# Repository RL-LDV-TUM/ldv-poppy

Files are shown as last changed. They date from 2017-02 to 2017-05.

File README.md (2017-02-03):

# LDV Poppy

The LDV Poppy is a customized version of the [Poppy Humanoid](https://www.poppy-project.org/en/robots/poppy-humanoid) by poppy-project.
The original Github repository containing the Solidworks 3D files and Software can be found [here](https://github.com/poppy-project/poppy-humanoid).
There is also a Onshape project where all Solidworks files are imported: [Poppy humanoid v1.0.1](https://cad.onshape.com/documents/77a0f84dc57f40418500cc3e/w/5e73b9c6a1ca45368c6251fc/e/ed6b82f994b249e388f92c2e).
This Onshape project can be cloned and edited. However it is sometimes easier to import only single Solidworks files from this repository to onshape.

## 3D Models

The Onshape project for the [LDV Poppy can be found here.](https://cad.onshape.com/documents/56d596aee4b004367d90f087/w/5446e589942f217504b25eb7/e/aac52fdb51e2f46d7fa4375f).
This project contains a full clone of the original Onshape project and the optimized files. Optimizations were nescessary to improve the 3D print outcome
on the Renforce RF1000 3D-Printer available at the LDV.
Currently there are still parts which need a redesign or can only be printed in a certain orientation: [Errors and Defects](3D/defects.md)

Instructions for printing can be found [here](3D/print.md).
Solidworks source files for editing: [solidworks](3D/solidworks)
STL files for printing: [stl](3D/stl)

## Programming

Poppy provides his own websever: [poppy.clients.ldv.ei.tum.de](http://poppy.clients.ldv.ei.tum.de)

Several *jupyter* notebooks are provided to controll the robot using the *odroid* mini PC.

Connecting poppy to the network: [Network](Software/network.md)

Getting started with poppy: [Working with poppy](Software/gettingStarted.md)

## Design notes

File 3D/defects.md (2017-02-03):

# Broken Parts
Most parts have a very tight fit. Therefore, some narrow structures break when higher tension occures. This happens because the space for the motors is too small or
the weight of the robot is to high. 

## Knee
The knee split up at a very narrow cover of the motor. This does not effect the payload because the part is held together by the motor itself.
However the crack does not look very nice.
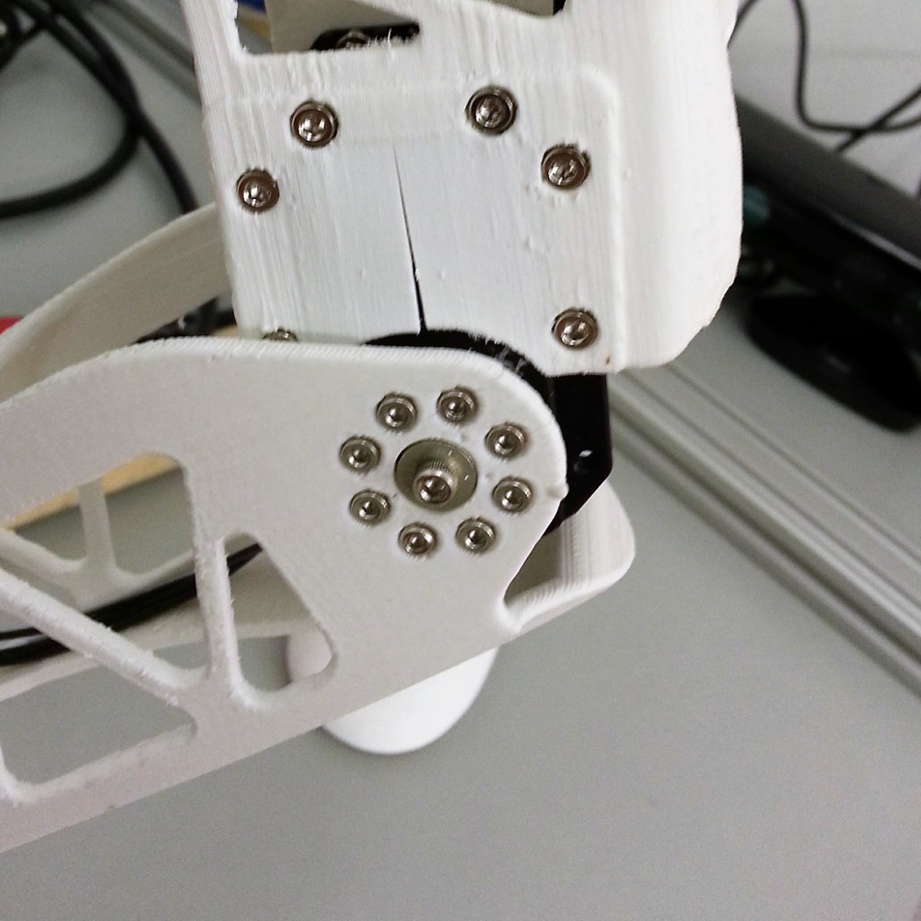
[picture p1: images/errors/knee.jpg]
Knee


On the other knee also the lower part has cracks in it. These were caused by the screws and an uneven print result.
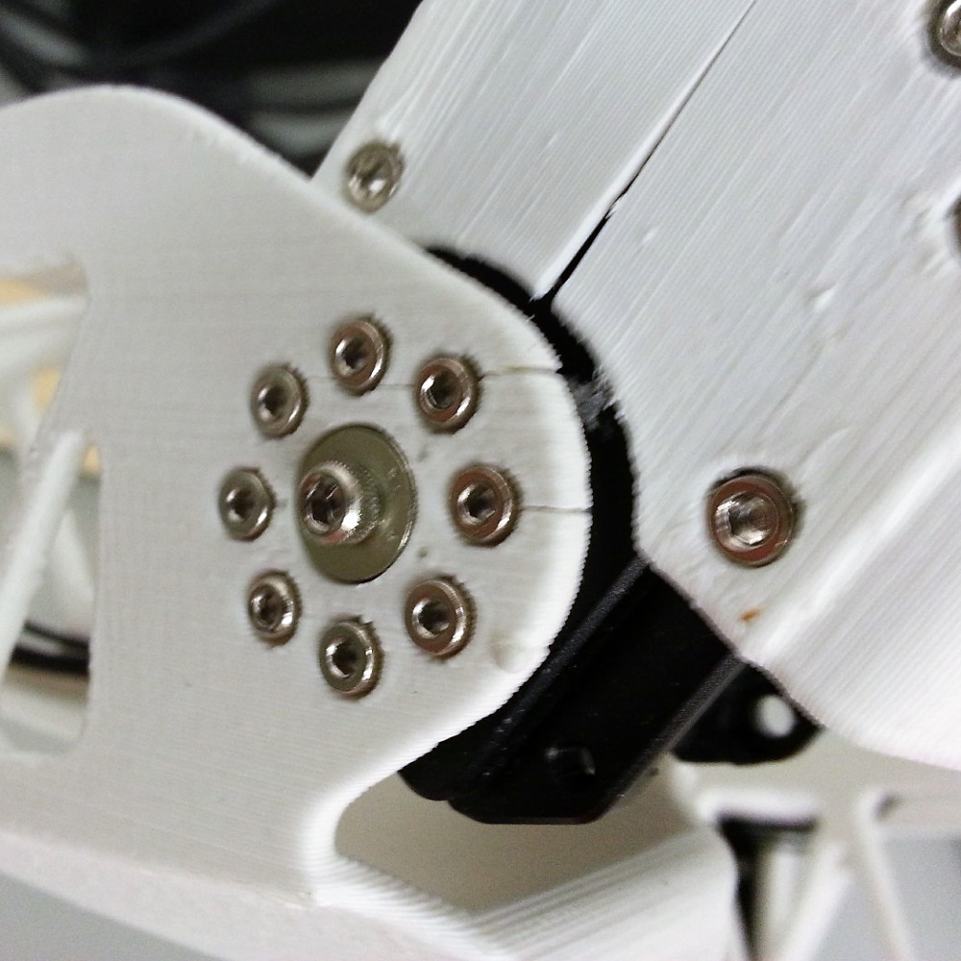
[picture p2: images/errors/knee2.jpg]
Knee2


## Ankle
The ankle has to be printed this way so that to motor plate fits through. Unfortunately, this causes the upper screws to be literally useless.
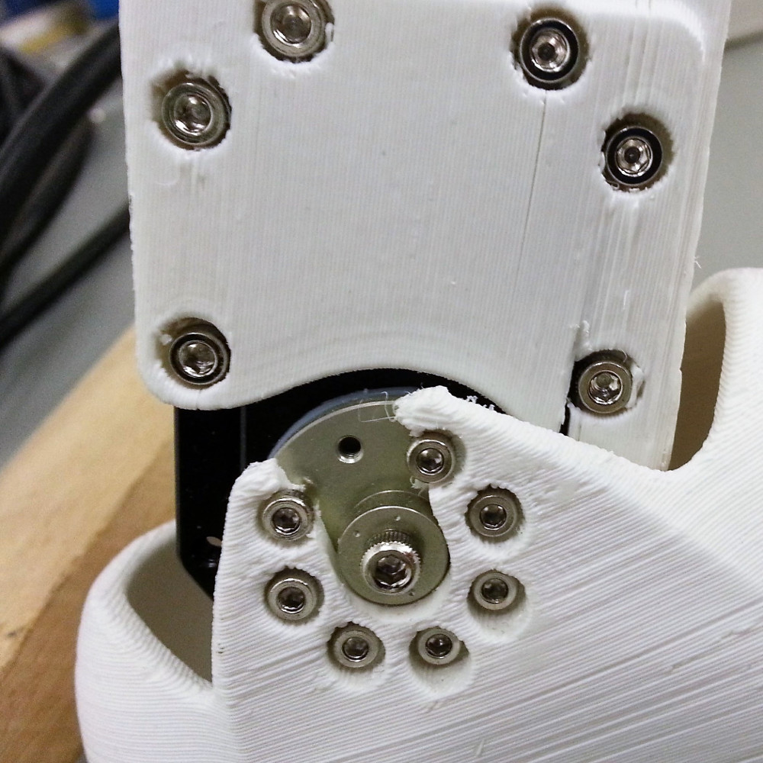
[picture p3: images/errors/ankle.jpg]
Ankle


## Pelvis
Due to hugh stress on this part, the pelvis broke in half at a printing layer. 
A new version of the pelvis is now employed in the robot which is 3mm thicker at each side.
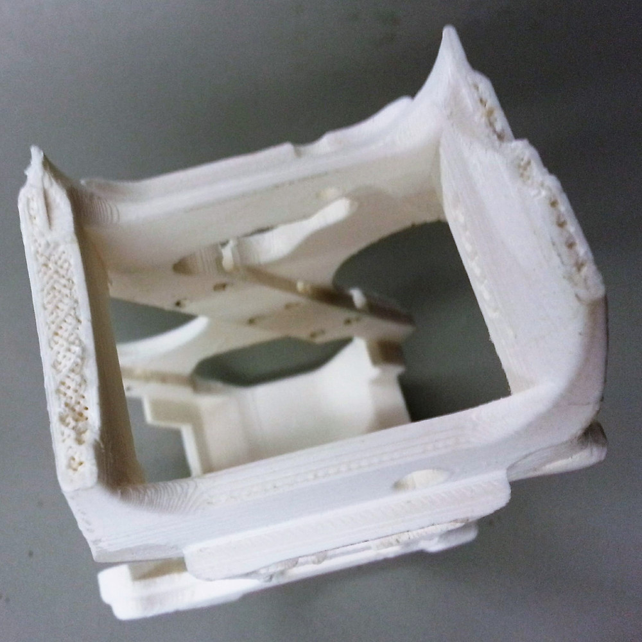
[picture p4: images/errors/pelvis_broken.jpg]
Pelvis


## Upper Arm
The upper arm suffered the same error as the knee. The narrow plate covering the motor was already thickened an reprinted.
The range of this plate is limited by the shouled part and can not be increased much further.

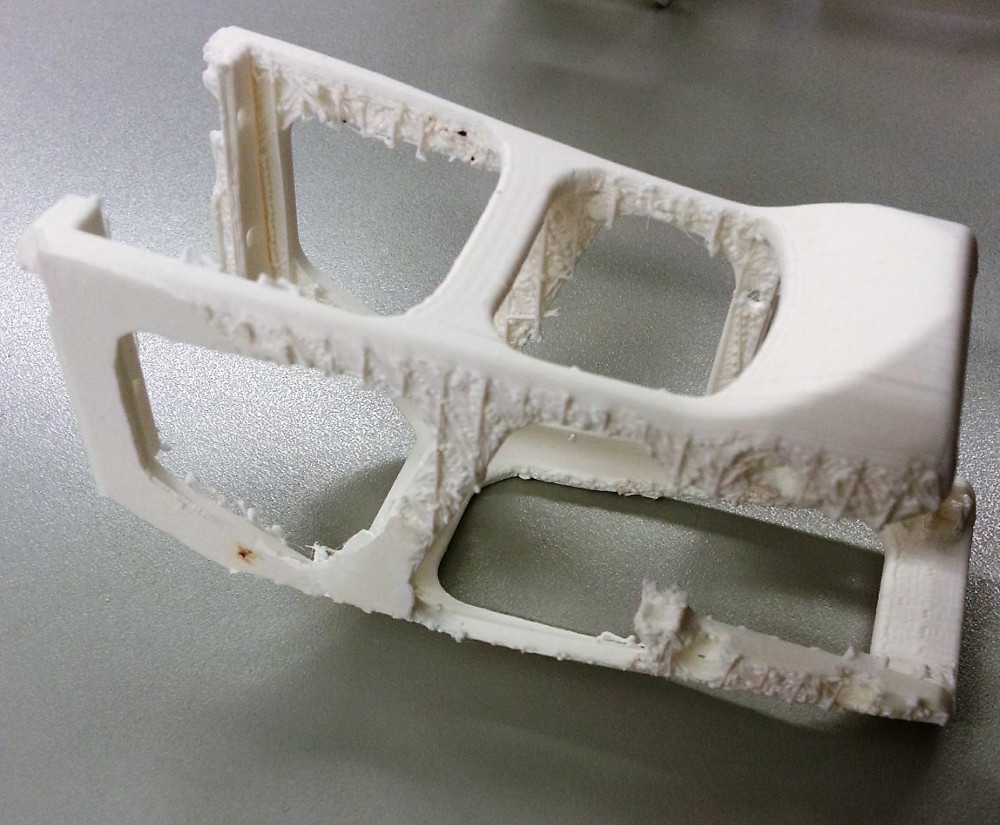
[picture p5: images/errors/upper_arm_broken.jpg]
Upper Arm


# Print Orientation
As the pelvis shows, printed parts are **vunerable where the filament layers are connected**. It is very unlikely that a layer itself will break.
Therefore, it is important that the object is printed in a way that later on no big forces will tear the different layers apart.
The main forces should never appear orthogonal to the layers, but alway **parallel**.

Unfortunately some parts are not feasable to be printed in that way.

## Chest
The chest is the biggest part of the robot. According to the forces it would be optimally printed standing upright.
Also the designers placed the grip in a way that the original model can not be printed lying without a huge amount of support strucutres.
The outcome of an upright print was not usable, so that the model had to be redesigned to be printed lying. 
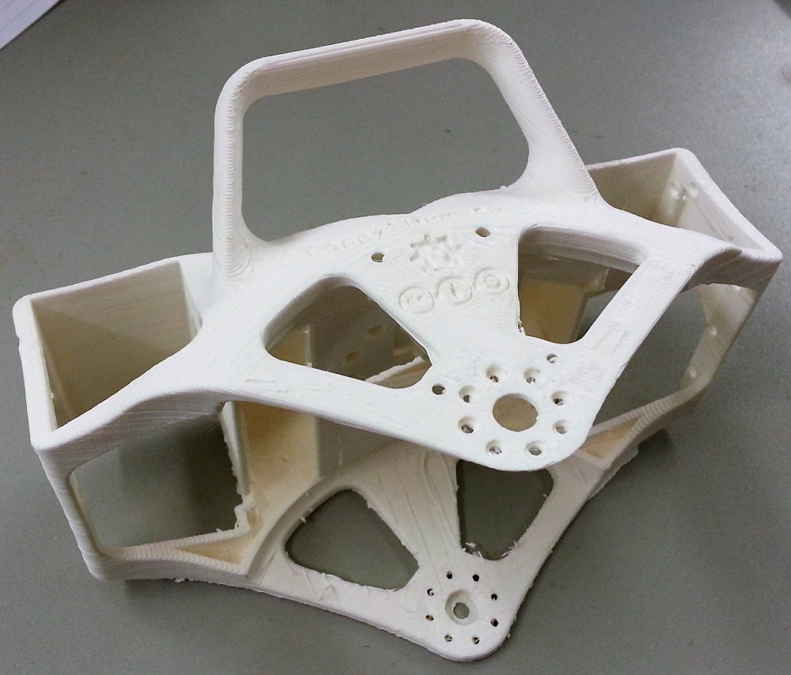
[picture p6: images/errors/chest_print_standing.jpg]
Chest

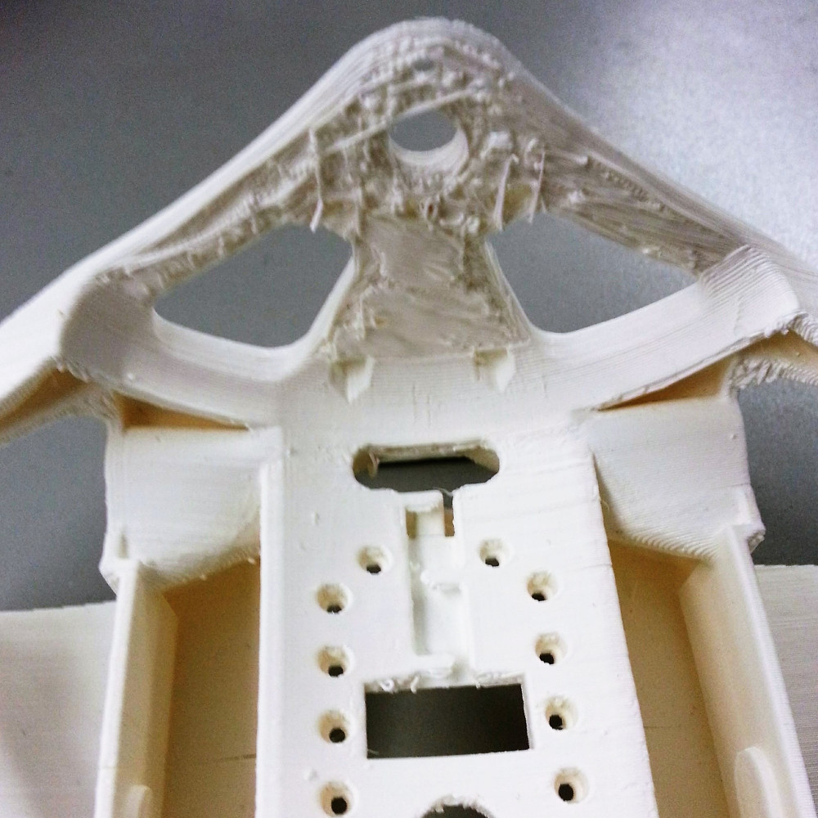
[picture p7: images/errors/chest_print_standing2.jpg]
Chest2


## Pelvis
The lying position has its advantages for the adhesion of the object.
The thin parts of the pelvis show that this is not feasable for this part.
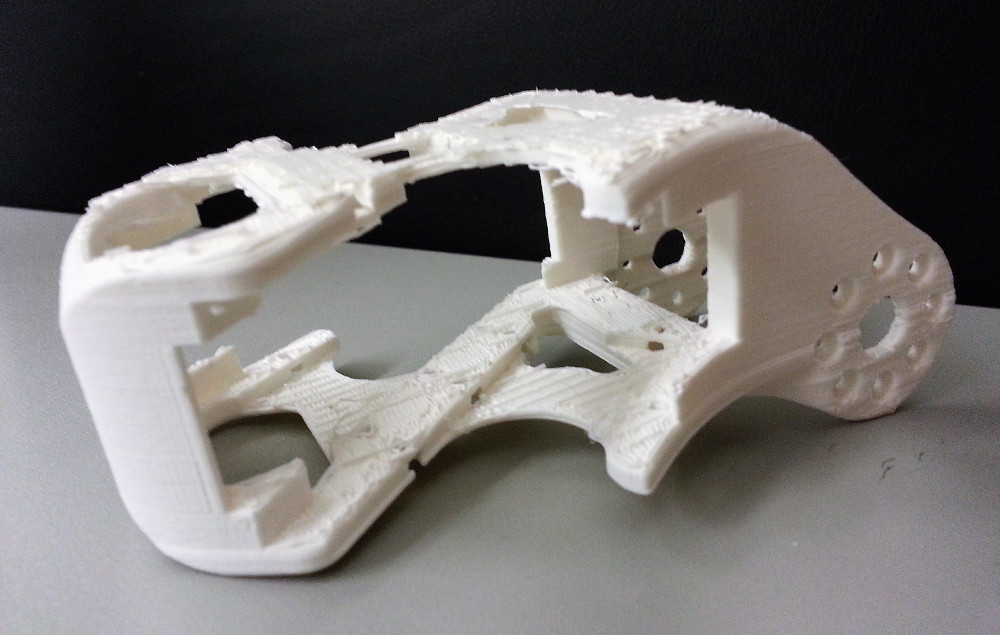
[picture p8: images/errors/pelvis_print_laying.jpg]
Pelvis


## Spine
One has to deal with the higher forces on the layers when the part is printed in the only possible standing position.
This can be done by increasing the thickness of the part where it does not affect the degrees of freedom of the motors.
The Spine before and after the increas of the outer walls.
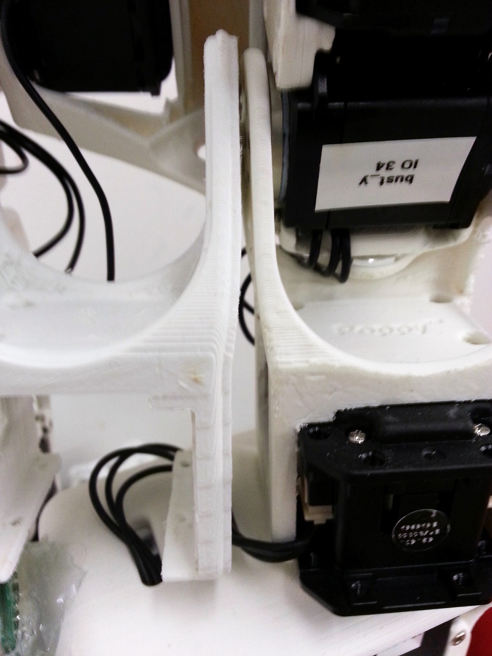
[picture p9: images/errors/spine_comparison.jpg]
Spine


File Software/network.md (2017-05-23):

# Ethernet

Poppy is configured to obtain a IP adress via DHCP when he is connected to the lrz network with an ethernet cable.
The DNS Service [poppy.clients.ldv.ei.tum.de](http://poppy.clients.ldv.ei.tum.de) is configured only for Wifi connections to the LDV-CPP network bridge.

# Wifi
Poppy automatically connects to the Wifi SSID: **LDV-CPP**

The LDV-CPP accesspoints work in bridge-mode so Poppy can be reached by: [poppy.clients.ldv.ei.tum.de](http://poppy.clients.ldv.ei.tum.de) 
This only works when the accesspoint is connected to the lrz network. 

    # interfaces(5) file used by ifup(8) and ifdown(8)
    # Include files from /etc/network/interfaces.d:
    source-directory /etc/network/interfaces.d
    
    auto eth2
    iface eth2 inet dhcp
    
    iface default inet dhcp
    
    auto lo
    iface lo inet loopback
    
    auto wlan2
    iface wlan2 inet dhcp
            wpa-ssid "LDV-CPP"
            wpa-psk "*******"
    
    allow-hotplug wlan2 eth2

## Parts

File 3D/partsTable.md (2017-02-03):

This table contains the settings which where used to print the current version of LDV-Poppy.

| 	| **Part Name** 	| **Resolution** 	| **Infill** 	| **Design Version** 	| **Units** 	| **Comment** 	|
|---	|---	|---	|---	|---	|---	|---	|
| **ARMS**  	| arm_connector 	| 0.2 	| 80 	| 1 	| 2 	| 	|
| 	| forearm_left 	| 0.2 	| 80 	| 1 	| 1 	| 	|
| 	| forearm_right 	| 0.2 	| 80 	| 1 	| 1 	| 	|
| 	| hand_left 	| 0.3 	| 80 	| 1 	| 1 	| 	|
| 	| hand_right 	| 0.3 	| 80 	| 1 	| 1 	| 	|
| 	| shoulder_left 	| 0.2 	| 80 	| 1 	| 1 	| 	|
| 	| shoulder_right 	| 0.2 	| 80 	| 1 	| 1 	| 	|
| 	| upper_arm 	| 0.2 	| 80 	| 2 	| 2 	| V2 is thickened at the narrow parts. Need for optimization is under investigation 	|
| **HEAD**  	| camera_support 	| 0.2 	| 80 	| 1 	| 1 	| 	|
| 	| fake_manga_screen 	| 0.3 	| 	| 1 	| 0 	| 	|
| 	| head_back 	| 0.3 	| 50 	| 2 	| 1 	| V2 has a wider cut-out in the back for a better port accessibility 	|
| 	| head_face 	| 0.3 	| 50 	| 1 	| 1 	| 	|
| 	| neck 	| 0.2 	| 80 	| 1 	| 1 	| 	|
| 	| screen 	| 	| 	| 1 	| 0 	| 	|
| 	| screen_support 	| 	| 	| 1 	| 0 	| 	|
| 	| speaker_left 	| 0.2 	| 50 	| 1 	| 1 	| 	|
| 	| speaker_right 	| 0.2 	| 50 	| 1 	| 1 	| 	|
| **LEGS**  	| hip_left 	| 0.2 	| 80 	| 1 	| 1 	| 	|
| 	| hip_right 	| 0.2 	| 80 	| 1 	| 1 	| 	|
| 	| hip_z_to_hip_y_connector 	| 0.2 	| 80 	| 1 	| 2 	| 	|
| 	| pelvis 	| 0.3 	| 50 	| 2 	| 1 	| 	|
| 	| shin 	| 0.2 	| 80 	| 1 	| 2 	| need for optimization, V1 breaks at narrow parts 	|
| 	| foot_left 	| 0.3 	| 50 	| 1 	| 1 	| 	|
| 	| foot_right 	| 0.3 	| 50 	| 1 	| 1 	| 	|
| 	| thigh_left 	| 0.3 	| 50 	| 1 	| 1 	| 	|
| 	| thigh_right 	| 0.3 	| 50 	| 1 	| 1 	| 	|
| **TRUNK** 	| abdomen 	| 0.2 	| 80 	| 	| 1 	| 	|
| 	| chest 	| 0.3 	| 30 	| 3 	| 1 	| V3 is tightened, This part takes ~22h to print 	|
| 	| i101_to_MX28_link 	| 0.2 	| 80 	| 1 	| 1 	| need for optimization 	|
| 	| i101_to_MX64_link 	| 0.2 	| 80 	| 3 	| 1 	| need for optimization 	|
| 	| MX28_double_rotation 	| 0.2 	| 80 	| 1 	| 1 	| 	|
| 	| MX64_double_rotation 	| 0.2 	| 80 	| 2 	| 1 	| 	|
| 	| spine 	| 0.2 	| 80 	| 2 	| 1 	| V2 is tightened because it is an important center part 	|

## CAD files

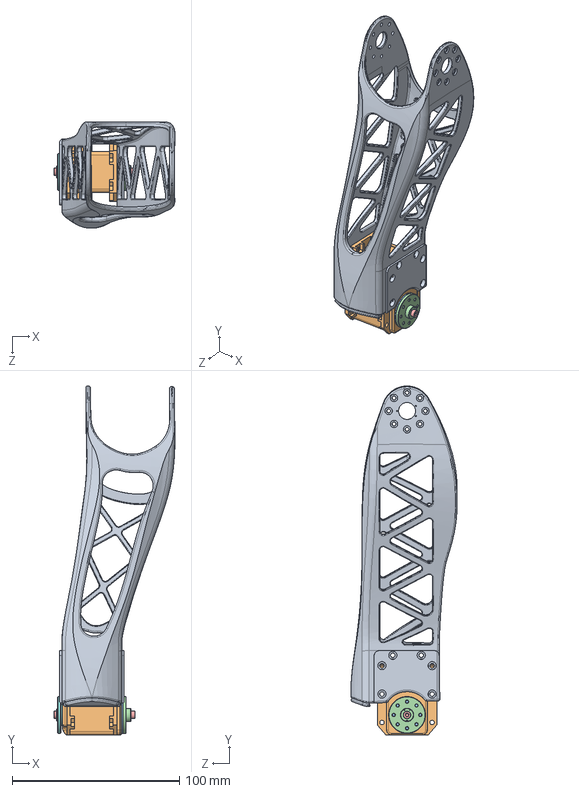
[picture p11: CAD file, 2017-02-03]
3D/solidworks/lower_limbs/subassemblies/thigh.SLDASM
72.3 x 208.9 x 63.7 mm
thigh
dynamixel_x28series
trust_washer
HN07-N101
WB_M2.5x8 x 2
RX28-CAP
MF106ZZ
HN07-i101
knee_bumper

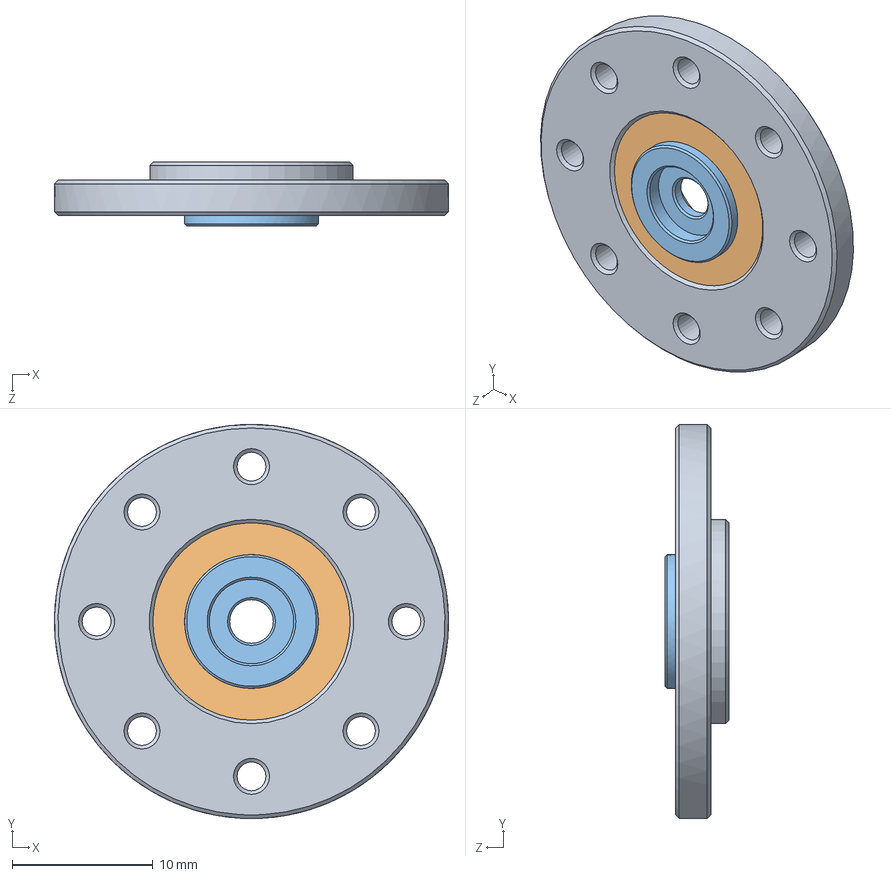
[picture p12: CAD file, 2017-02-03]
3D/solidworks/robotis_library/bearing/i101_Set.SLDASM
28.0 x 28.0 x 4.56 mm
HN05-i101
MF128ZZ
RX64-CAP

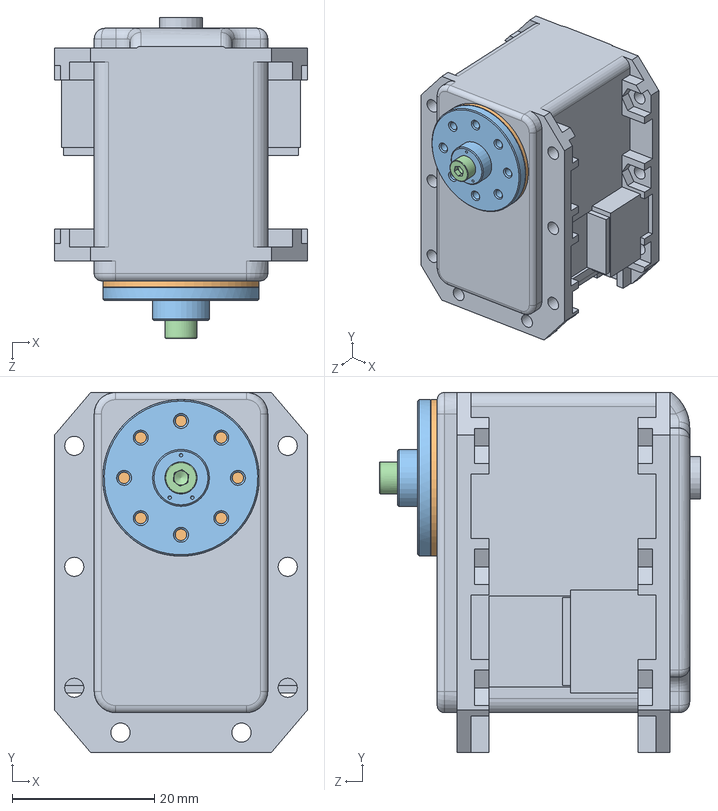
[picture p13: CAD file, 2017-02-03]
3D/solidworks/robotis_library/MX-28.SLDASM
35.6 x 50.6 x 45.1 mm
dynamixel_x28series
trust_washer
HN07-N101
WB_M2.5x8

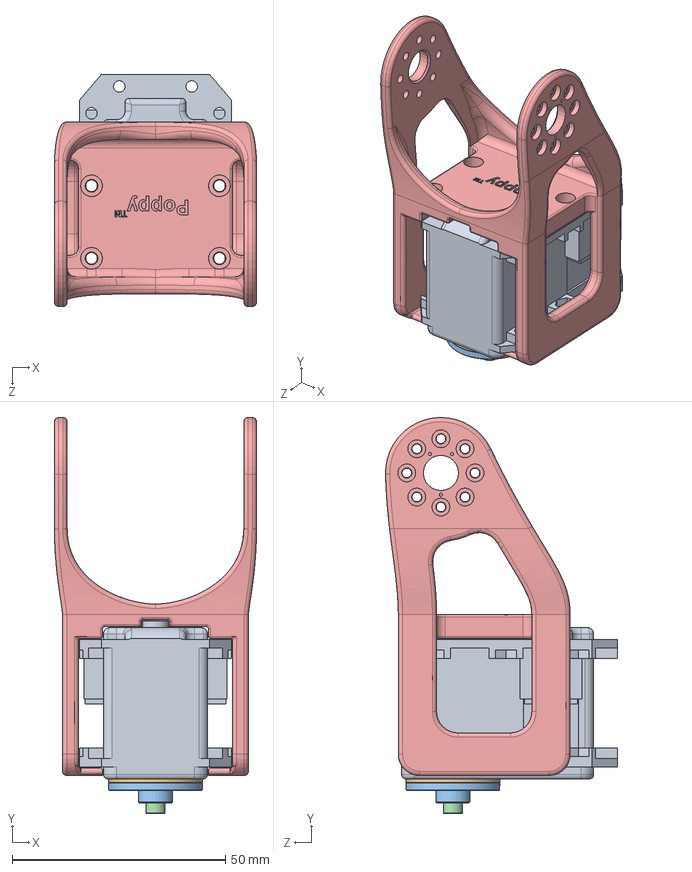
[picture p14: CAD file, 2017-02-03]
3D/solidworks/torso/subassemblies/spine.SLDASM
47.4 x 92.8 x 54.4 mm
dynamixel_x28series
trust_washer
HN07-N101
WB_M2.5x8
spine

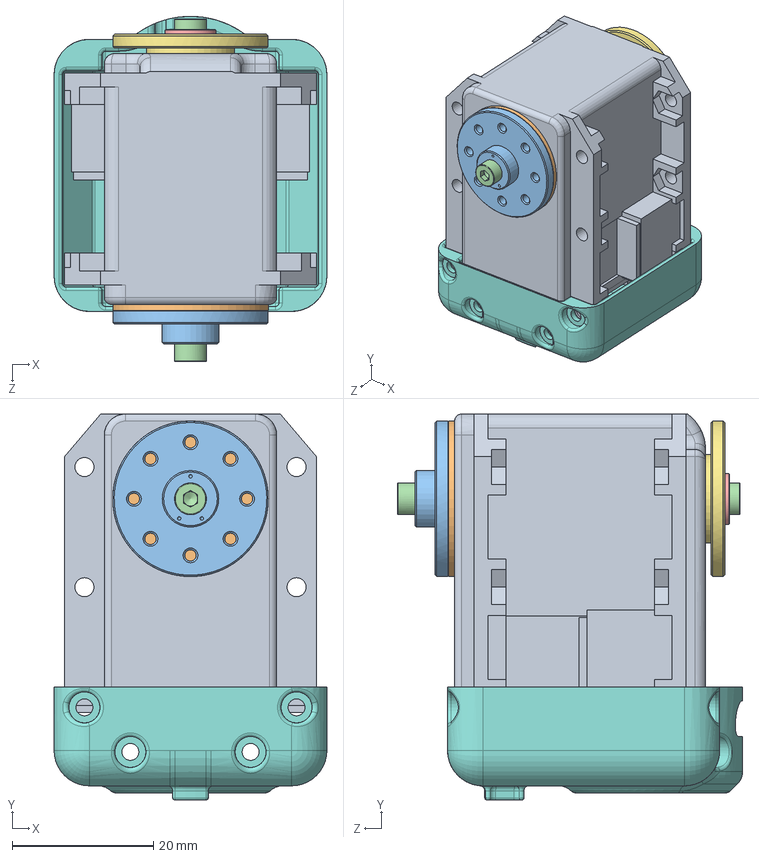
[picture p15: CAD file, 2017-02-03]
3D/solidworks/upper_limbs/subassemblies/shoulder_x.SLDASM
38.6 x 54.6 x 48.8 mm
dynamixel_x28series
trust_washer
HN07-N101
WB_M2.5x8 x 2
RX28-CAP
MF106ZZ
HN07-i101
arm_connector

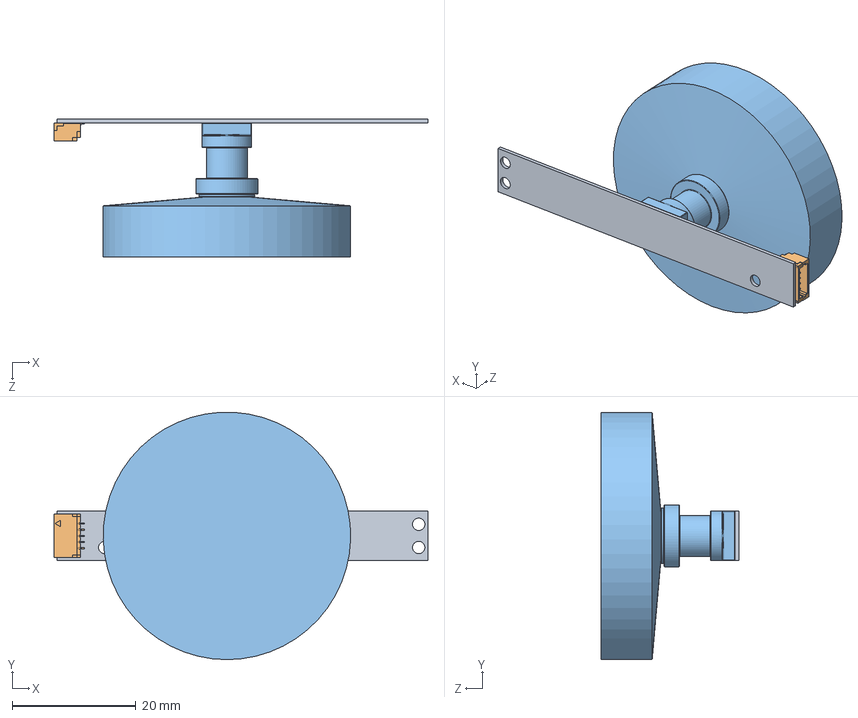
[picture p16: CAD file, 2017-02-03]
3D/solidworks/head/embedded_components/camera/Videw_JDEPC-OV04.SLDASM
60.5 x 40.0 x 22.3 mm
Videw_JDEPC-OV04
SM05B-SRSS-TB
170_FOV_lens

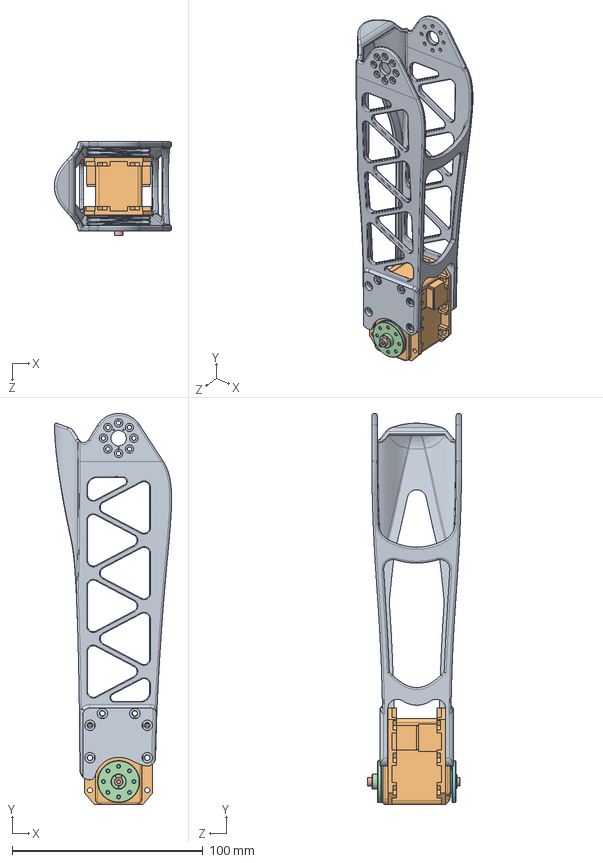
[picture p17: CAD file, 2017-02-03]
3D/solidworks/lower_limbs/subassemblies/shin.SLDASM
61.5 x 205.0 x 49.3 mm
shin
dynamixel_x28series
trust_washer
HN07-N101
WB_M2.5x8 x 2
RX28-CAP
MF106ZZ
HN07-i101

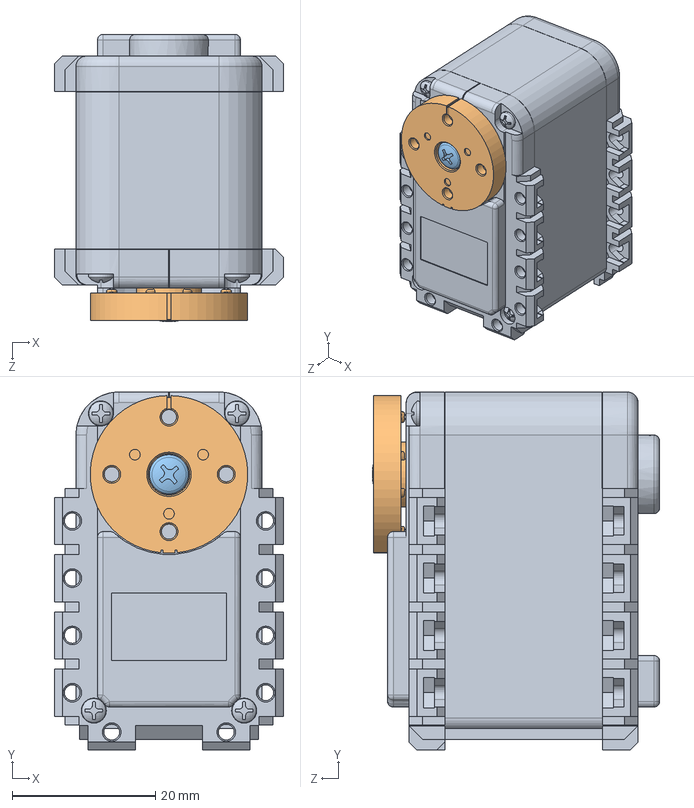
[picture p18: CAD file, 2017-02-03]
3D/solidworks/robotis_library/AX-12_18A.SLDASM
32.0 x 50.0 x 40.1 mm
dynamixel_AXseries
AX12_horn
BHS_M2_6X8

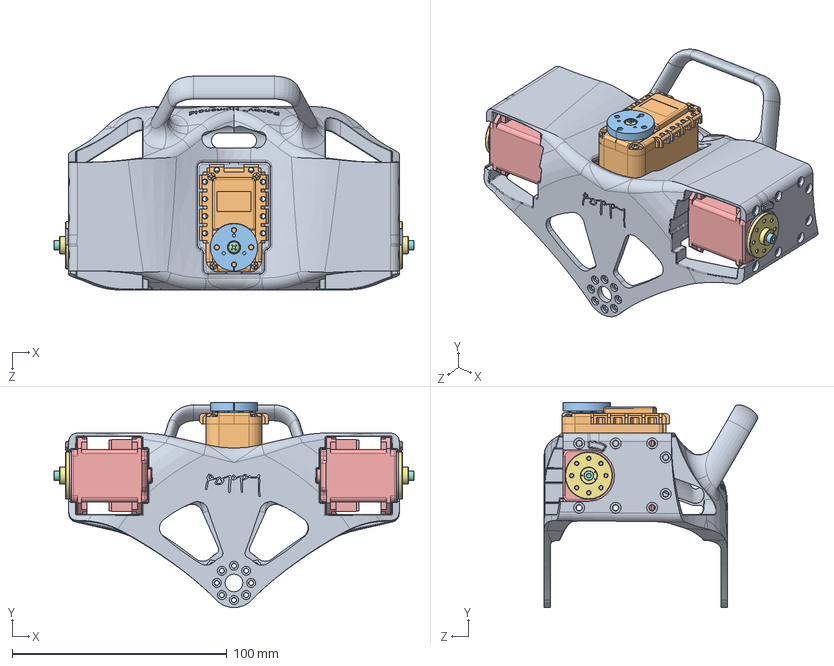
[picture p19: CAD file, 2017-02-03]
3D/solidworks/torso/subassemblies/chest.SLDASM
167.7 x 95.6 x 99.5 mm
chest
dynamixel_AXseries
AX12_horn
BHS_M2_6X8
dynamixel_x28series x 2
trust_washer x 2
HN07-N101 x 2
WB_M2.5x8 x 2

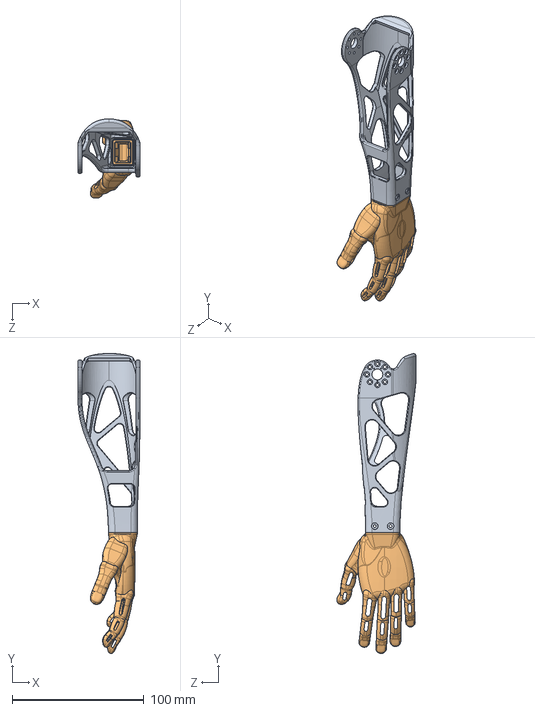
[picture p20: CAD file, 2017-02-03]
3D/solidworks/upper_limbs/subassemblies/forearm.SLDASM
47.0 x 227.5 x 60.1 mm
forearm
hand

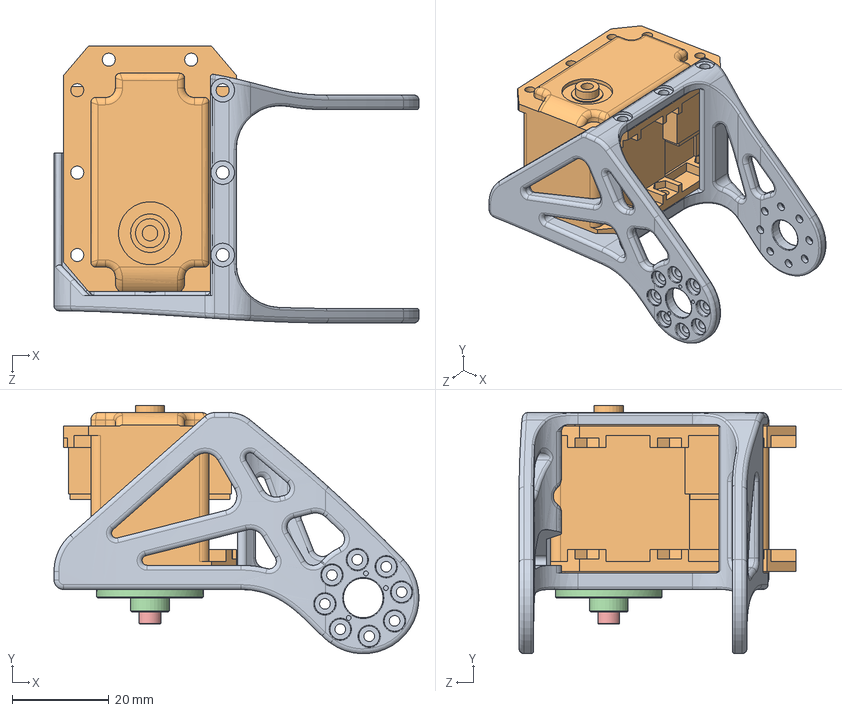
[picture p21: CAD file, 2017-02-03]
3D/solidworks/lower_limbs/subassemblies/hip.SLDASM
75.3 x 51.2 x 57.1 mm
hip
dynamixel_x28series
trust_washer
HN07-N101
WB_M2.5x8

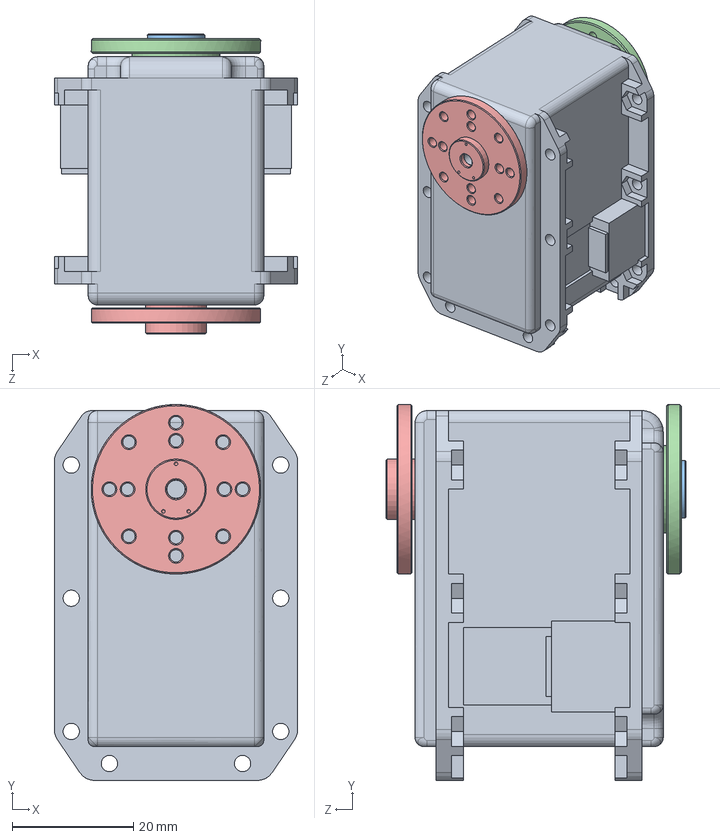
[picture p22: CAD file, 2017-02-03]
3D/solidworks/robotis_library/MX-64.SLDASM
40.2 x 62.1 x 49.6 mm
dynamixel_x64series
MF128ZZ
RX64-CAP
HN05-i101
HN05-N101

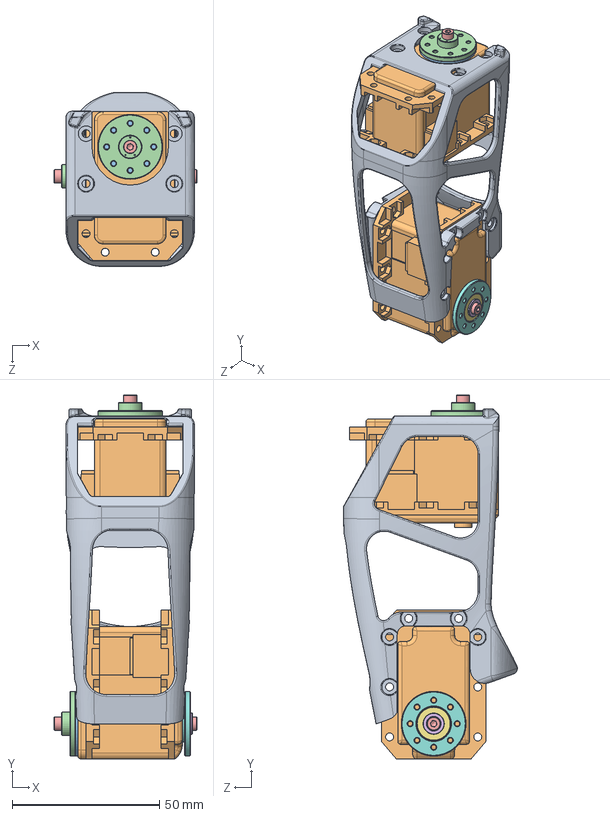
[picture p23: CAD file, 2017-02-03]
3D/solidworks/upper_limbs/subassemblies/upper_arm.SLDASM
48.5 x 123.8 x 59.1 mm
upper_arm
dynamixel_x28series x 2
trust_washer x 2
HN07-N101 x 2
WB_M2.5x8 x 3
RX28-CAP
MF106ZZ
HN07-i101

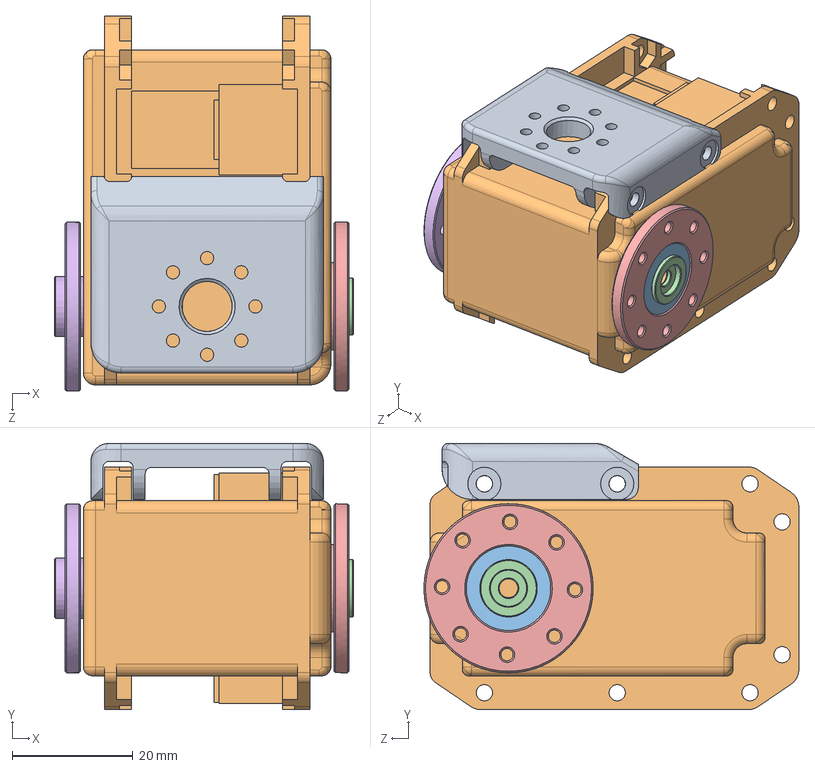
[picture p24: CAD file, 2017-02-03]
3D/solidworks/lower_limbs/subassemblies/hip_main_motor.SLDASM
49.6 x 44.1 x 62.1 mm
hip_z_to_hip_y-connector
dynamixel_x64series
MF128ZZ
RX64-CAP
HN05-i101
HN05-N101

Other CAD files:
3D/solidworks/robotis_library/double_rotation.SLDASM
3D/solidworks/lower_limbs/subassemblies/pelvis.SLDASM
3D/solidworks/head/embedded_components/camera/SM05B-SRSS-TB.SLDPRT
3D/solidworks/head/embedded_components/computer/Odroid_U3.SLDPRT
3D/solidworks/head/embedded_components/camera/170_FOV_lens.SLDPRT
3D/solidworks/head/embedded_components/camera/65_FOV_lens.SLDPRT
3D/solidworks/head/embedded_components/camera/Videw_JDEPC-OV04.SLDPRT
3D/solidworks/head/embedded_components/display/fake_manga_screen.SLDPRT
3D/solidworks/head/embedded_components/imu/Hardware/9DOF-Razor-v23.SLDPRT
3D/solidworks/head/embedded_components/speaker/VisatonK20.40_speaker.SLDPRT
3D/solidworks/head/parts/camera_support.sldprt
3D/solidworks/head/parts/neck.SLDPRT
3D/solidworks/head/parts/screen.sldprt
3D/solidworks/head/parts/screen_support.sldprt
3D/solidworks/head/parts/speaker_left.sldprt
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

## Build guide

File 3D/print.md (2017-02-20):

# Print

## 3D Models

The *.STL* files for all parts are contained in the [stl](/3D/stl) folder, respectively the *.SDLPRT* (Solidworks Source Files) are in the [solidworks](3D/solidworks) folder.
As noted in the [Parts Table](3D/partsTable.md) not all parts are needed to print the LDV-Poppy.
Furthermore there are redesigned versions of some parts, which are more durable or more comfortable to assemble. 
The newest version is documented in the [Parts Table](3D/partsTable.md)

## Software
The Software which is used to bring the 3D files to the printer is Repetier Host.
Before the first use of Repetier Host with a new printer make sure that the programm has the right printer settings.

### Object Placement
You can easily drag a *.STL* or *.OBJ* file into the main windown of Repertier Host to add this object to the print job.
In order to find the right orientation to print the object refer to [Print Orientation](3D/defects.md#print-orientation) on the defects site.

### Slicer
The best tuned slicer for this project was curaengine. Make sure that curaengine is selected before changing any other thing in the slicer configuration.
All slicer configuration files can be found in the [PrinterSettings](3D/PrinterSettings) folder.
Use *cura_poppy_300* as Print Configuration. If you use ABS as filament select *ABS_poppy1* as Filament Setting for Extruder 1.
Choose the *PLA_poppy1* in the case you use PLA material.
Detailed settings for each object can be found in the [Parts Table](3D/partsTable.md)

## Printer Settings
Settings for using Repetier Host with the RF1000

Connections Tab:

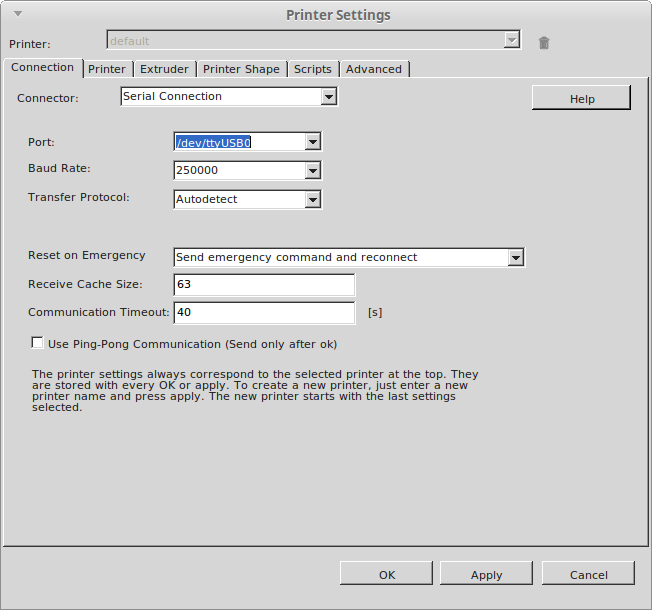
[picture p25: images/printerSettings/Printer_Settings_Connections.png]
Connections


Extruder Tab:

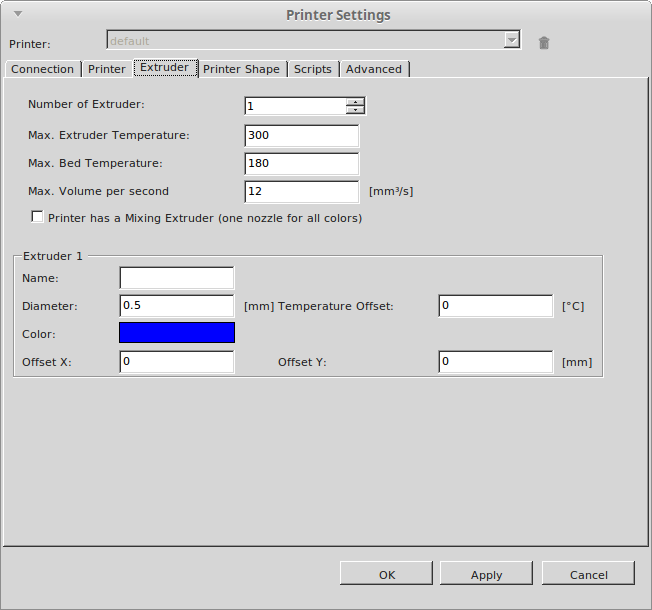
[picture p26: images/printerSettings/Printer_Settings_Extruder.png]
Extruder


Printer Tab:

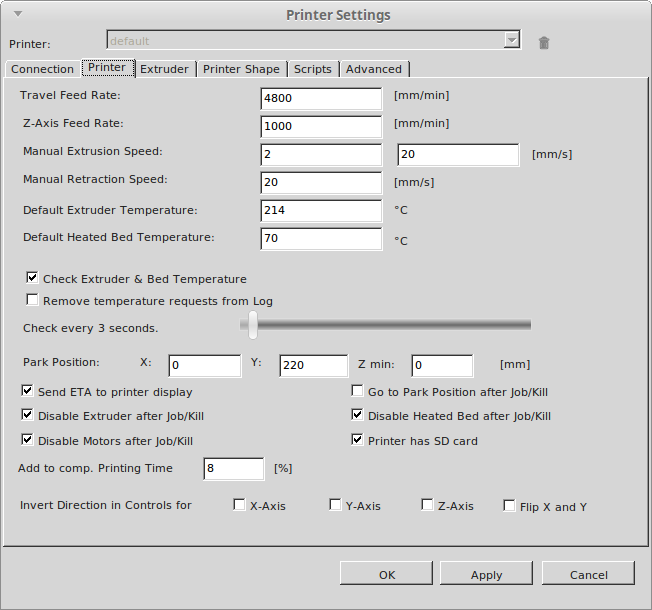
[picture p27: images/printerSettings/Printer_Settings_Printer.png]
Printer


PrinterShape Tab:

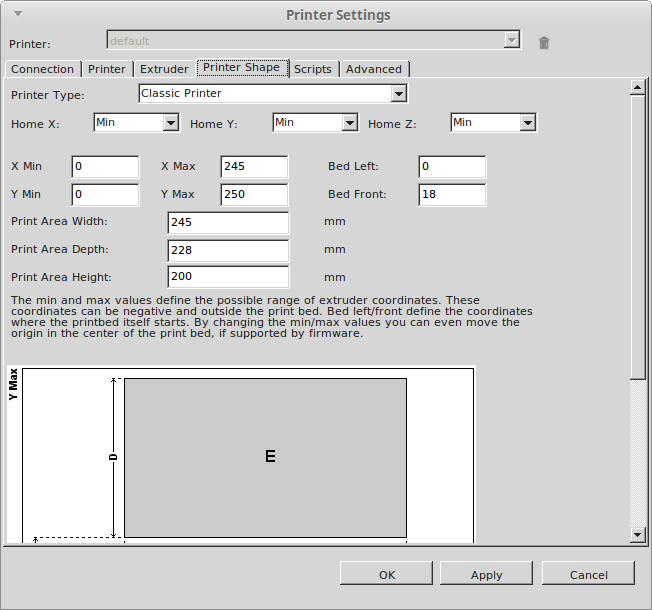
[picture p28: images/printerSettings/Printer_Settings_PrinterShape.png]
PrinterShape


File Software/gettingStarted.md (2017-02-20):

# Connecting with Poppy

Open your browser and connect to poppy's webserver: [poppy.clients.ldv.ei.tum.de](http://poppy.clients.ldv.ei.tum.de)

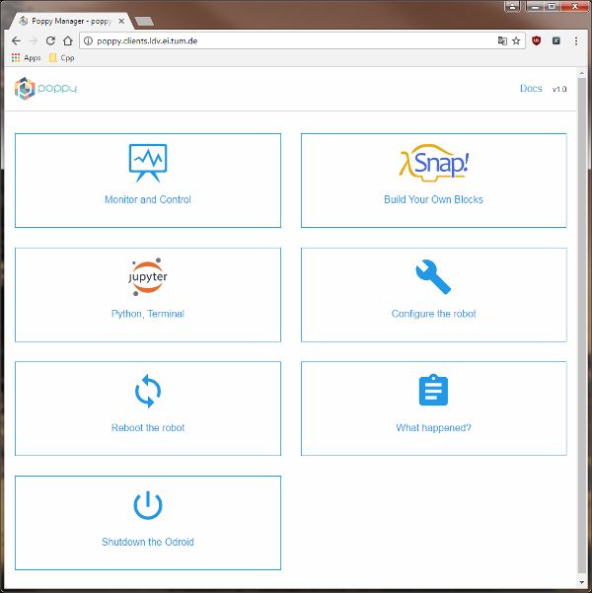
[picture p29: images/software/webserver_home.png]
Webserver Home


Poppy can be programmed in SNAP and Python. For python choose Jupyter:

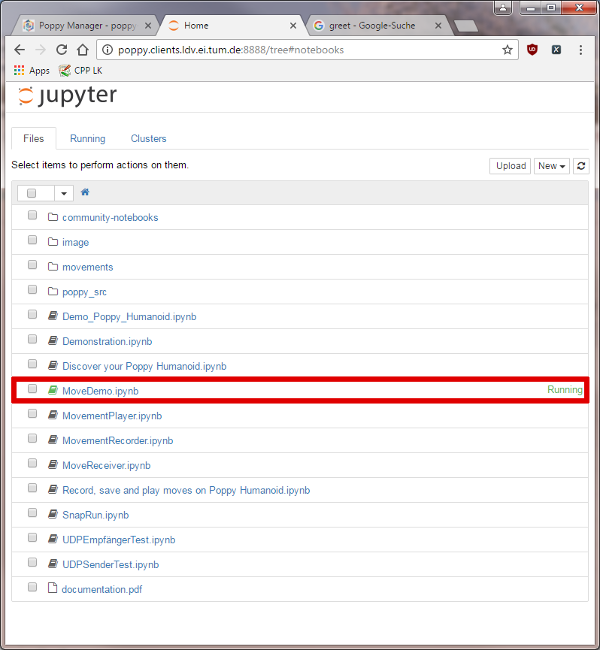
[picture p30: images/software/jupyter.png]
Jupyter


A good demo file to show some moves is: [MoveDemo](Software/moveDemo.md)

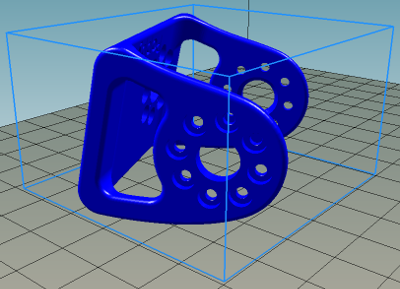
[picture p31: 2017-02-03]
images/print/print_shoulder.png

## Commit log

2017-02-06 Added arm_connector_V2.stl
2017-02-07 Enhanced and strengthened upper_arm_V3.stl
2017-04-05 fixed wrong namings, deleted incorrect part
    [simple_foot_left.STL, simple_foot_right.STL]
2017-04-05 added print settings and part list for poppy2
